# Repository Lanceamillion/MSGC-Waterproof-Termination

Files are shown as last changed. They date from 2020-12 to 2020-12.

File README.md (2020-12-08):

# MSGC-Waterproof-Termination
#### Waterproof Inline Flight Termination System for Ocean Bound High Altitude Balloons
Files and Documentation for "V3" Waterproof Balloon Termination System

Designed by:
- Andy Kirby
- Tim Uhlenbruck
- Lance Nichols
- Isaac Schmidt

### Abstract
This project sought to develop an inline flight termination system capable of surviving in damp and intermittently submerged conditions. These conditions would allow for this device's use in ocean bound flights and flights that start or fly through rain storms. 

### Waterproofing
The waterproof box was designed to be easily 3D printed in three parts. Two lids with O-ring grooves and counterbores for bolts on one lid and for nuts on the other that lie outside of the O-ring grooves. The main housing of the box has two shelves on either side for the cut down board to be bolted to. It also features holes for the bolts to pass through as well as a hole on the side to allow a seatbelt to be tied to the box. The final detail is the two holes on opposite ends intended to be taped so two nylon compression fittings (1/8” NPT - 1/4” tube Parker 2GUW3) can be screwed in. A 9/16” diameter silicon septum is cut from 1/8” thick 50A durometer silicone sheeting and inserted inside the nut of the compression fitting. A sewing awl is used to insert a length of waxed string through the septa.  When the awl needle is withdrawn the hole produced shrinks back forming a waterproof seal between the septa and the line.  Waxed thread is used to keep water from wicking down the fibers in the line and into the enclosure.

### Hardware
The PCB notably features a channel that contains the line against the attached nichrome wire. 80-34 gauge nichrome is suspended 0.1” between two terminals and is driven with a MOSFET making it red hot and severing the line. The system utilizes the XBEE 3 Micro for both radio and microcontroller purposes. This along with the improvements in reduction of components improved the size of the board. One 1.5V AAA battery is employed as the power source, along with a boost converter to achieve the 3.3V required for the XBEE. 

### Software
The software is written in MicroPython with little complexity, appropriate for its purpose. The program monitors the radio for the cutdown command and sets the MOSFET pin high for ten seconds when it is received. The program also ensures that the MOSFET is not run more than once per command sent from the ground team.

### Control
The system receives the command to cut down over a local XBEE 3 radio network. During testing, this command was sent from a central payload containing an Iridium satellite modem. The modem in turn received commands from the Iridium satellite network which were uplinked by the ground team.

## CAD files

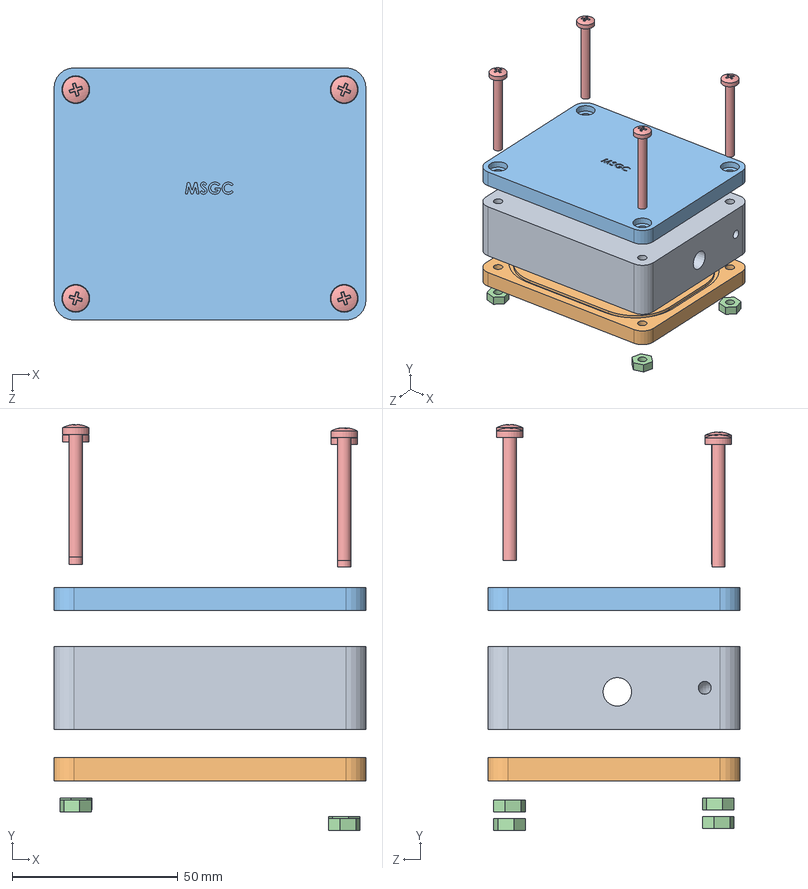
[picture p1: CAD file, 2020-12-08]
Box Hardware/SolidWorksFiles/Water Proof Box.SLDASM
94.0 x 122.3 x 76.0 mm
two sided Box 2.1
two sided Lid A3
two sided Lid B3
Nut x 4
Screw x 4

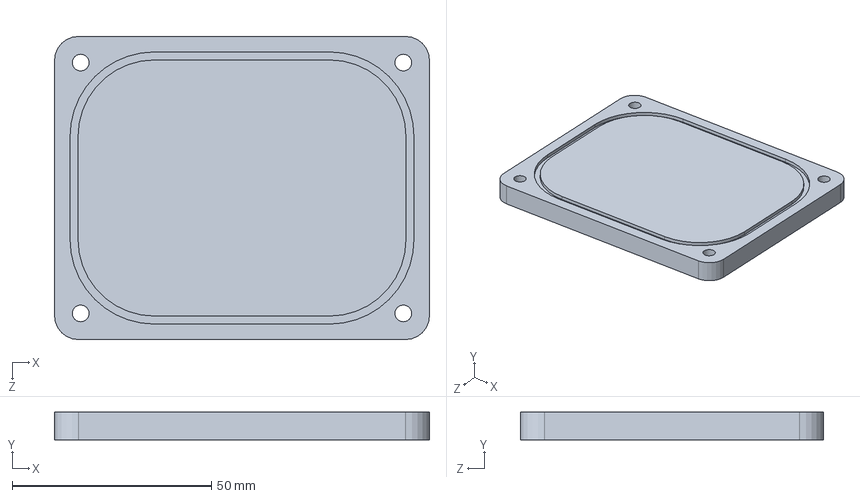
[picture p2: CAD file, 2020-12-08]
Box Hardware/SolidWorksFiles/two sided Lid A3.SLDPRT
94.0 x 7.00 x 76.0 mm

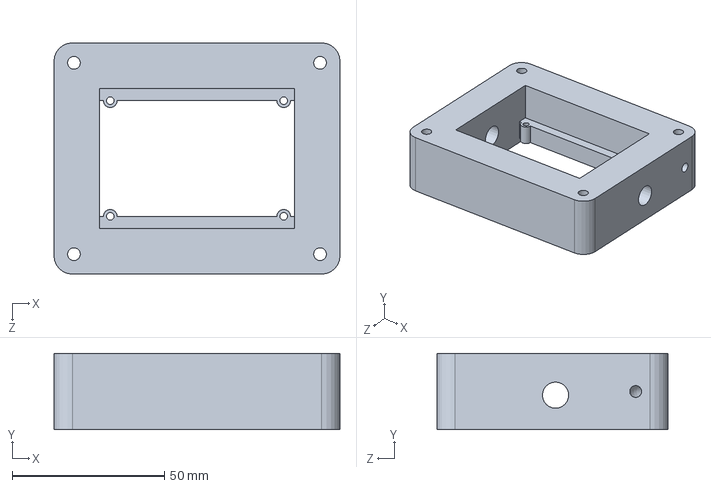
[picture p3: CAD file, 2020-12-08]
Box Hardware/SolidWorksFiles/two sided Box 2.1.SLDPRT
94.0 x 25.0 x 76.0 mm

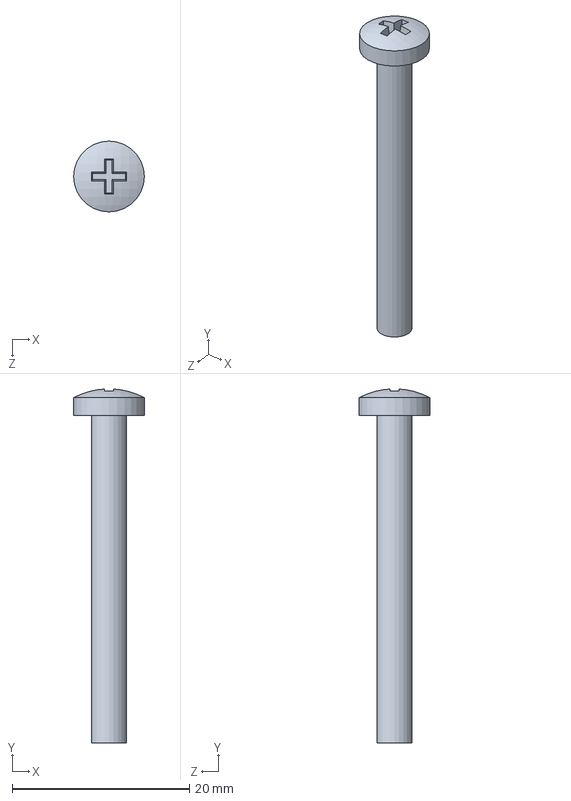
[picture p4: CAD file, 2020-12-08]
Box Hardware/SolidWorksFiles/Screw.SLDPRT
8.00 x 40.0 x 8.00 mm

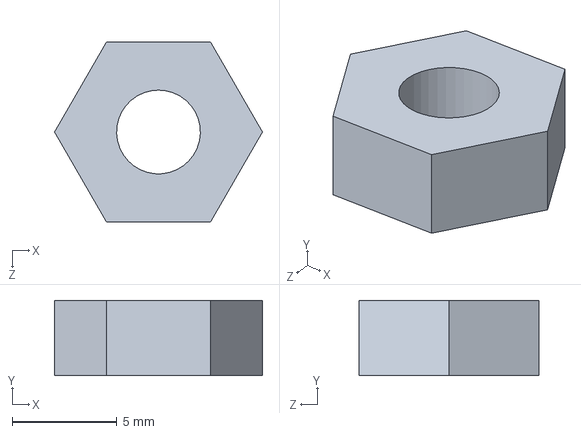
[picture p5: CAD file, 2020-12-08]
Box Hardware/SolidWorksFiles/Nut.SLDPRT
9.93 x 3.60 x 8.60 mm

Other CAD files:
Box Hardware/SolidWorksFiles/two sided Lid B3.SLDPRT
Box Hardware/STLs/two sided Box 2.1.STL
Box Hardware/STLs/two sided Lid A3.STL
Box Hardware/STLs/two sided Lid B3.STL

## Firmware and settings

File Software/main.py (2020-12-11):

import xbee
import time
# from sys import stdin, stdout
import machine
from machine import Pin
# from machine import UART
# from pyb import UART


# ~~~~~~~~~~~~~~~~~~~~ FUNCTION DEFINITIONS ~~~~~~~~~~~~~~~~~~~~~~~~~~~~~~~~~~
# Flush the buffer because we have just handled code
def flush_rx_buffer():
    for i in range(100):
        xbee.receive()

def pri_cutdown():
    global priCutdownFlag
    print("PRI CUTDOWN RECEIVED")
    if(priCutdownFlag):
        priCutdownFlag = False
        print("PRI CUTDOWN INITIATED")
        PRI_MOSFET.value(1)
        ASSOC_LED.value(1)
        flush_rx_buffer()
        time.sleep(20)
        PRI_MOSFET.value(0)

def idle_command():
    global priCutdownFlag
    global secCutdownFlag
    priCutdownFlag = True
    priCutdownFlag = True
    ASSOC_LED.value(0)

def check_for_command(payload):
    print("Checking for command")
    # Parse bytes as a string
    payload = payload.decode("utf-8")
    # Take out first 3 characters
    if len(payload) >= 3:
        command = payload[0] + payload[1] + payload[2]
        print("Interpretted command: " + command)
        if "JKL" == command:
            pri_cutdown()
        elif "ABC" == command:
            idle_command()
            print("IDLE")

# ~~~~~~~~~~~~~~~~~~~~~~~~~~~~~~~~~~~~~~~~~~~~~~~~~~~~~~~~~~~~~~~~~~~~~~~~~~~~

print('ID: ' + str(xbee.atcmd('MY')))
# PIN DEFINITIONS
USER_LED = Pin(machine.Pin.board.D4, Pin.OUT, value=0)
PRI_MOSFET = Pin(machine.Pin.board.D12, Pin.OUT, value=0)
ASSOC_LED = Pin(machine.Pin.board.D5, Pin.OUT, value=0)

# FLAG DEFINITONS
priCutdownFlag = True
secCutdownFlag = True

while True:
    packet = xbee.receive()
    #print(packet)
    if packet != None:
        print(packet.get('payload'))
        check_for_command(packet.get('payload'))
    USER_LED.value(1)
    time.sleep(0.2)
    USER_LED.value(0)
    time.sleep(0.2)

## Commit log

2020-12-08 Upload CAD
    [Nut.SLDPRT, Screw.SLDPRT, Water Proof Box.SLDASM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]
2020-12-08 Added STLs
    [two sided Box 2.1.STL, two sided Lid A3.STL, two sided Lid B3.STL]
